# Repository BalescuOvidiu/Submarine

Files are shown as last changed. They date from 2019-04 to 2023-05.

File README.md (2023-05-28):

# Submarin dronă - Clasa Metere

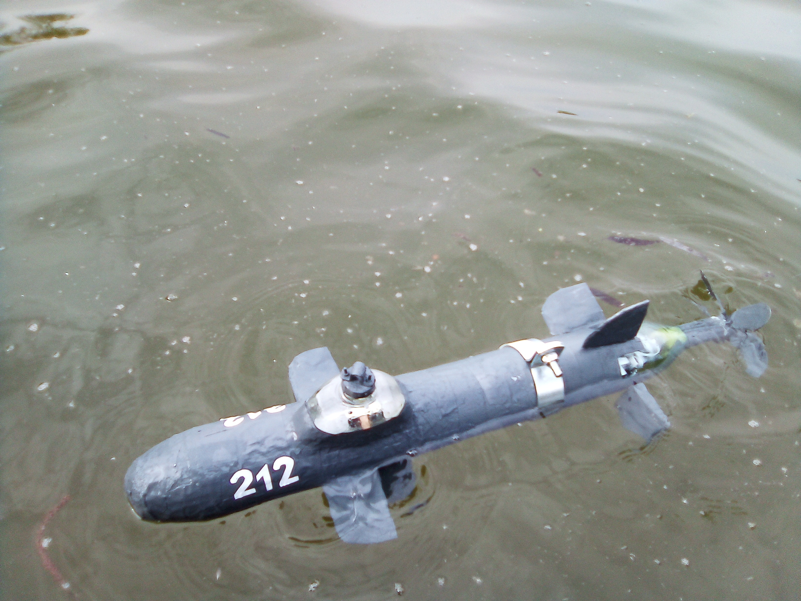
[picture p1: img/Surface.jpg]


## Cuprins

1. [Despre proiect](https://github.com/BalescuOvidiu/Submarine#despre-proiect)<br>
3. [Caracteristici generale](https://github.com/BalescuOvidiu/Submarine#caracteristici-generale)<br>
2. [Structură](https://github.com/BalescuOvidiu/Submarine#structură)<br>
5. [Circuit electric](https://github.com/BalescuOvidiu/Submarine#circuit-electric)<br>
5. [Software](https://github.com/BalescuOvidiu/Submarine#software)<br>
6. [Viitoare îmbunătățiri](https://github.com/BalescuOvidiu/Submarine#viitoare-îmbunătățiri)<br>
7. [Versiuni](https://github.com/BalescuOvidiu/Submarine#versiuni)<br>
7. [Unități](https://github.com/BalescuOvidiu/Submarine#unități)<br>
7. [Teste](https://github.com/BalescuOvidiu/Submarine#teste)<br>
8. [Rezultate](https://github.com/BalescuOvidiu/Submarine#rezultate)<br>

## Despre proiect

<p align = "justify">
Acest proiect e reprezentat de un tip de vehicul mic capabil să meargă prin apă, controlate printr-o telecomandă sau cu un laptop. Scopul acestuia este de a explora spațiul acvatic, de găsi obiecte pierdute în apă sau pentru divertisment.
</p>
<p align = "justify">
O dronă, este un vehicul căruia îi lipsește pilotul uman, fiind ghidat fie de către un pilot automat digital aflat la bordul său, fie prin telecomandă. Un submarin este un vehicul capabil să meargă prin apă la diverse adâncimi și să se ridice la suprafață. Vehiculul acestui proiect este un submarin dronă. 
</p>

## Caracteristici generale

| Nume clasă &nbsp; &nbsp; &nbsp; &nbsp; &nbsp; | Metere  &nbsp; &nbsp; &nbsp; &nbsp; &nbsp; &nbsp; &nbsp; &nbsp; &nbsp; &nbsp; &nbsp; &nbsp; | 
|:---|:---|
| Cost unitate | 2422.34 RON |
| Deplasament | La suprafață: 5.9 kg  <br> În imersie: 7.8 kg |
| Lungime | 102.5 cm |
| Lățime | 10.0 cm |
| Pescaj | 7.5 cm |
| Propulsie | 1 <a href = "https://www.pololu.com/category/60/micro-metal-gearmotors"> motor DC cu reductor 50:1 HPCB 6 V </a><br>1 <a href = "https://en.wikipedia.org/wiki/Pump-jet"> elice cu 7 lame pompă-jet</a> |
| Viteză | 5.2 noduri (9.7 km / h) |
| Autonomie | 3.5 ore |
| Adâncime operațională | 0.5 m (1.6 ft) fără cablu <br> 3.0 m (9.6 ft) cu cablu |
| Adâncime maximă | 10.0 m (65.6 ft) |
| Rază acoperire comunicații | 1000 m (3280.8 ft) la suprafață |
| Sensori și sisteme de procesare | 2 <a href = "https://www.optimusdigital.ro/ro/compatibile-cu-arduino-nano/1686-placa-de-dezvoltare-compatibila-cu-arduino-nano-atmega328p-i-ch340.html" >plăci de dezvoltare Arduino Nano v3</a> <br> 1 <a href = "https://www.optimusdigital.ro/ro/ism-24-ghz/119-modul-nrf24l01-pentru-distante-mari.html" >transceiver nRF24L01</a> <br>1 <a href = "https://www.optimusdigital.ro/ro/senzori-senzori-inertiali/865-modul-senzor-cu-9-axe-mpu9250.html" >IMU MPU9250</a> <br>3 <a href = "https://www.optimusdigital.ro/ro/senzori-senzori-ultrasonici/2943-modul-senzor-ultrasonic-rezistent-la-apa-jsn-sr04t-cu-sonda-pt-masurare-la-distana.html" >senzori de distanță JSN-SR04T</a> |
| Alimentare  | 32 <a href = "https://www.soselectronic.ro/products/conrad-energy/4aa2500mwh1-6v-bp4-1-153207">acumulatori AA de 1.6 V, 1500 mAh</a>  |

## Structură

<p align = "justify">
Denumirea clasei vine de la numele celor două materiale principale folosite la construirea corpului interior: metal(oțel în cazul nostru) și polietilenă tereftalată (PET). Principiul de construire constă în combinarea metalului și plasticului astfel încât structura să fie cât mai rezistentă și cât mai ușoară. Oțelul e rezistent, dar greu și oxidabil. Polietilena tereftalată e ușoară, flexibilă, nu ruginește, dar fragilă.
</p>
<p align = "justify">
PET-ul este o masă plastică folosită de obicei la fabricarea diverselor ambalaje, care în cele din urmă ajung gunoi și contaminează apa cu microplastic. Totuși aceasta poate fi folosită pentru a proteja câteva circuite de apa rece a mării, iar o structură metalică poate oferi o rezistență deosebită ambalajului de plastic.
</p>
<p align = "justify">
Carcasa submarinul este construită din PET și este acoperită cu silicon. Același principiu este aplicat, elicei, cârmelor și hidroplanelor. Siliconul e mult mai rezistent față de cauciuc sau de vopsea și este mult mai ecologic în sensul că nu interacționează cu apa și nu lasă în urmă particule.
</p>
<p align = "justify">
Structura este modulară pentru a fi ușor de reparat. Fiecare compartiment este alcătuit din două capace metalice conectate cu 4 colțare așezate în formă de cruce. Fiecare colțar este conectat cu cel de pe celălalt capac cu o placă de oțel zincat de îmbinare. Toată structura compartimentului este acoperită cu o folie de PET îmbinată de structura metalică cu șuruburi, formând un cilindru sau o semi-sferă. Fiecare compartiment se poate deschide în partea de sus. Cele două capace metalice ale compartimentului au 8 găuri pentru îmbinarea cu alte compartimente și încă 2 găuri pentru fire. Compartimentele sunt conectate cu 4 plăci de îmbinare zincate. Ca si sigilant s-a folosit silicon. Acesta e biodegradabil și rezistent la apă.
</p>

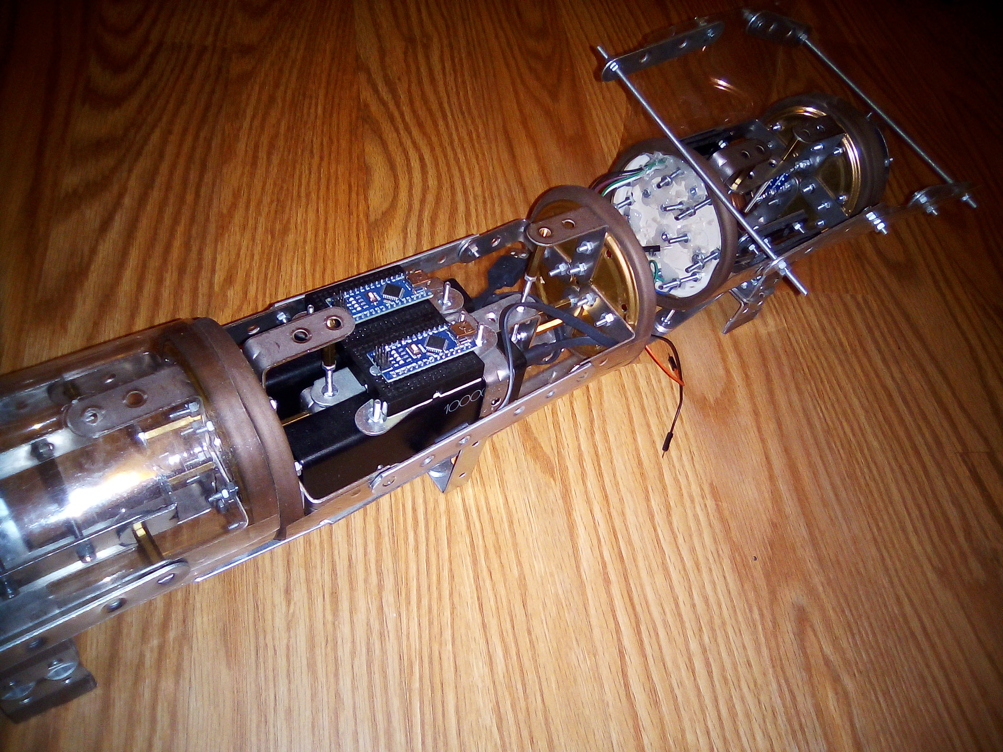
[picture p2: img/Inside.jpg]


#### Compartimente

| &nbsp; &nbsp; # | Compartiment &nbsp; &nbsp; &nbsp; &nbsp; &nbsp; &nbsp; &nbsp; &nbsp; &nbsp; &nbsp; &nbsp; &nbsp; | &nbsp; &nbsp; # | Compartiment &nbsp; &nbsp; &nbsp; &nbsp; &nbsp; &nbsp; &nbsp; &nbsp; &nbsp; &nbsp; &nbsp; &nbsp; &nbsp; &nbsp; &nbsp; &nbsp; &nbsp; &nbsp; |
|----:|:---|----:|:---|
| 1 | Pupa | 5  | Alimentare și circuit central |
| 2 | Compartiment servomotoare | 6  | Control hidroplane față și sistem de orientare |
| 3 | Alimentare circuit motoare și servomotoare | 7  | Provă |
| 4 | Compartiment utilitar | 8  | Corpul de navigare | 

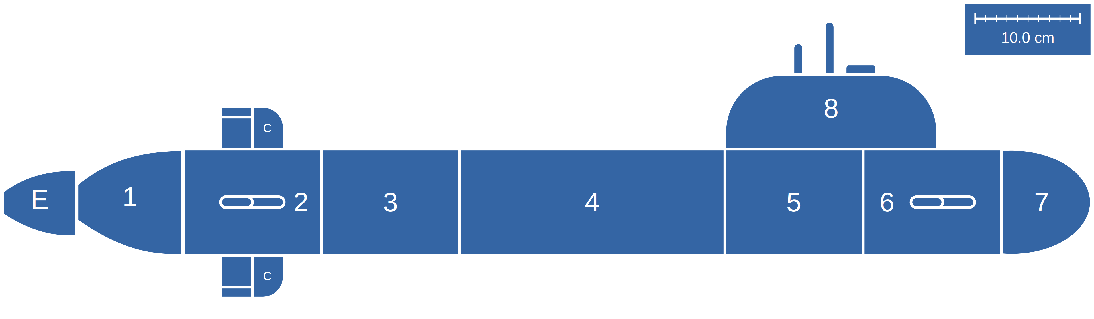
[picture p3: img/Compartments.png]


## Circuit electric
<p align = "justify">
Sunt două surse de alimentare: spate și față. Ambele au un voltaj de 6.0 V. Fiecare sursă este formată din 4 socluri conectate în paralel. Fiecare soclu are 4 acumulatori AA conectați în serie de 1.6 V, 1500 mAh.
</p>
<p align = "justify">
Cele două plăci Arduino sunt alimentate de sursa din față. Alimentarea pentru plăci poate fi oprită sau pornită dintr-un comutator. Senzorii și modulele auxiliare sunt conectate la sursele de alimentarea al celor două plăci Arduino, la 3.3 V sau 5.0 V în funcție de nevoi. Motoarele sunt conectate la sursa din spate, mai puțin servomotorul din față care e alimentat de sursa din față. Alimentarea motoarelor este controlată printr-un tranzistor pentru fiecare. Tranzistorul primește semnal de la placa Arduino dacă să oprească sau să pornească alimentarea.
</p>

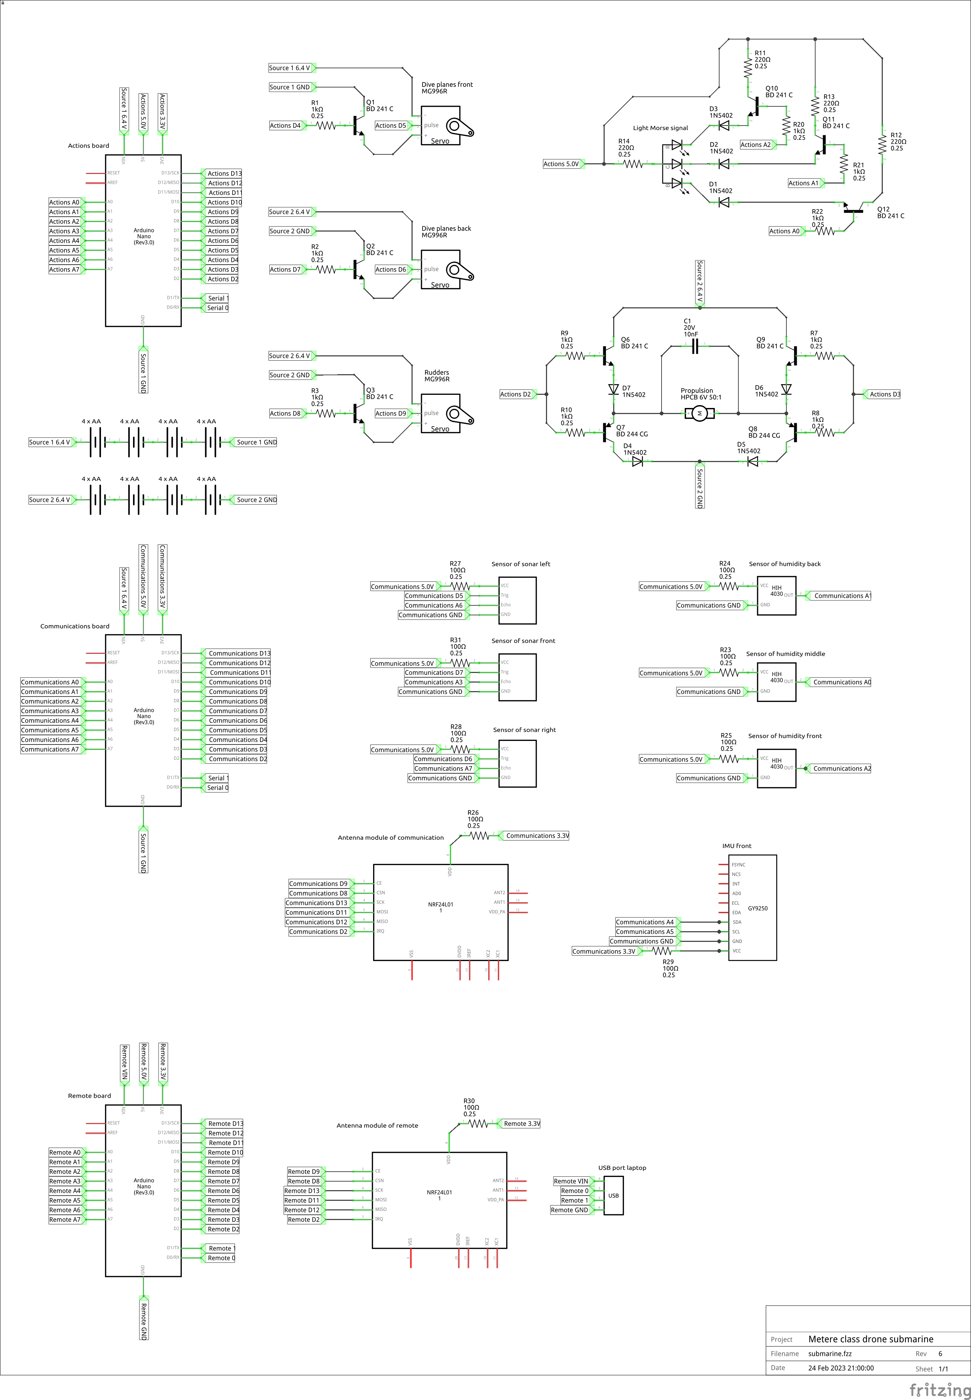
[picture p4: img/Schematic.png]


## Software
<p align = "justify">
Programele pentru plăcile <a href = "https://www.arduino.cc/">Arduino</a> de pe vehicul și telecomandă au fost scrise în C++ pentru arhitectura ARV, microcontrolere.</p>
<p align = "justify">
Interfața grafică a fost scrisă în limbajul <a href = "http://www.cplusplus.com/">C++ 11</a> și au fost folosite framework-urile: <a href = "https://www.sfml-dev.org/">SFML 2.5.1</a> și <a href = "https://github.com/nlohmann/json">Nlohmann JSON</a>. Aceasta are scopul de a vizualiza datele de la senzorii submarinului și de controla componentele de pe acesta.</p>

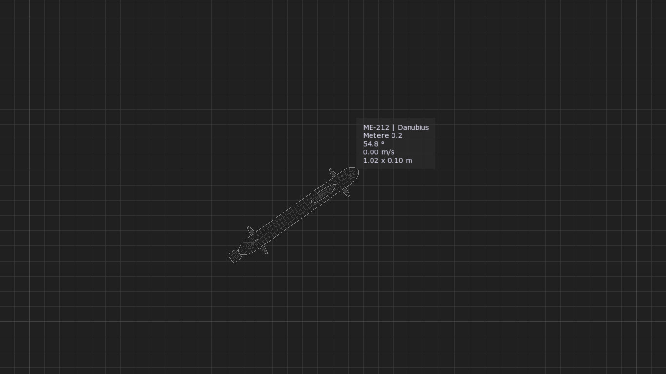
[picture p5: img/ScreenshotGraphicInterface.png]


#### Cerințe minime sistem pentru interfață
1. Procesor DualCore 2.0 GHz,
2. DDR2 RAM 2G,
3. Placă video 256MB,
4. Sistem de operare Linux, Windows sau Mac. 

## Viitoare îmbunătățiri
1. Optimizare și îmbunătățire software,
2. Optimizare consum de energie,
3. Extindere rază și adâncime acoperire comunicații,
4. Instalare cameră pe corpul de navigare,
5. Instalare generator din cupru și aluminiu pentru alimentarea acumulatorilor.

## Versiuni

| # | Data | Descriere |
|--:|:---|:---|
| 0.2 | 20 Octombrie 2019 | Compartimentele au fost restructurate și etanșate separat. Carcasa din PET a fost reconstruită și acoperită cu silicon. La fel și aripile. Propulsia cu elice 7 lame a fost înlocuită cu elice cu 7 lame pompă-jet.<br> Servomotoarele <a href="https://www.optimusdigital.ro/ro/motoare-servomotoare/271-servomotor-mg90s.html">MG90S</a> montate anterior au fost înlocuite cu <a href="https://www.optimusdigital.ro/ro/motoare-servomotoare/1160-servomotor-metalic-digital-mg996.html">MG996</a> și s-a adăugat unul pentru planele de scufundare din față. <br> Receptorul infrarosu a fost înlocuit cu un modul <a href = "https://www.optimusdigital.ro/ro/ism-24-ghz/119-modul-nrf24l01-pentru-distante-mari.html" >transceiver nRF24L01</a>. Bateriile AA de 1.5V au fost înlocuite cu <a href = "https://www.soselectronic.ro/products/conrad-energy/4aa2500mwh1-6v-bp4-1-153207">acumulatori AA de 1.6 V, 1500 mAh</a>. <br> S-au adăugat: trei senzori de umiditate pentru detectatarea scurgeriilor, un sistem pe bază de tranzistori bipolari de putere pentru controlul surselor de alimentare al motoarelor, un <a href = "https://www.optimusdigital.ro/ro/senzori-senzori-inertiali/865-modul-senzor-cu-9-axe-mpu9250.html" >IMU MPU9250</a> și 3 senzori ultrasonici de distanță <a href = "https://www.optimusdigital.ro/ro/senzori-senzori-ultrasonici/2943-modul-senzor-ultrasonic-rezistent-la-apa-jsn-sr04t-cu-sonda-pt-masurare-la-distana.html" >JSN-SR04T</a>. |
| 0.1 | 1 Ianuarie 2019 | Prima versiune. |

## Unități

<p align = "justify">
În momentul actual proiectul este în faza experimentală și se urmărește dezvoltarea doar unei singure unități.
</p>

| # | Nume | Versiune | Lansare | Începerea construcției | Dezvoltator | Status |
|:----|:---|:---|:---|:---|:---|:---|
| ME-212 | Danubius | 0.1 | 16 Aprilie 2019 | 1 Ianuarie 2019 | Bălescu Ovidiu-Gheorghe | În construcție pentru a trece la versiunea 0.2 |

## Teste

#### Testare versiunea 0.1 - 16 Aprilie 2019 
<p align = "justify">
S-a desfășurat pe lacul din Parcul Tineretului, București. S-a deplasat fără probleme la suprafața apei, dar nu a reușit să execute o submersie. 
Problema era cauzată de planele de scufundare din față, fiind fixate(nu erau conectate la un motor, ci doar lipite). Asta nu a permis să încline submarinul cu botul în jos și să execute o submersie dinamică. Carcasa din PET acoperită cu lac de lemn nu a permis apei să intre, dar în urma unor șocuri mecanice s-a observat că lacul întărit se desprinde de pe plastic.
Click <a href = "https://drive.google.com/file/d/1TcdASmKPXG35pqwhGr6TglmWBqajAN5j/view?usp=share_link" >aici</a> pentru a vedea filmarea. 
</p>

## Rezultate

#### Proiect la cursul de Introducere în Robotică, anul universitar 2018 - 2019

| Universitatea București &nbsp; &nbsp; &nbsp; &nbsp; &nbsp; &nbsp; &nbsp; &nbsp; &nbsp; &nbsp; &nbsp; &nbsp; &nbsp; &nbsp; | Facultatea de Matematică și Informatică &nbsp; &nbsp; &nbsp; &nbsp; &nbsp; &nbsp; &nbsp; &nbsp; &nbsp; &nbsp; &nbsp; &nbsp; &nbsp; &nbsp; &nbsp; &nbsp; &nbsp; |
|:---|:---|
| Profesor coordonator | Dumitriu Andrei |
| Laborant | Octavia Ivona |
| Student | Bălescu Ovidiu-Gheorghe |
| Notă evaluare | 10 / 10 |

#### Proiect prezentat la Sesiunea de comunicări Științifice Studențești - 2019

| Universitatea București &nbsp; &nbsp; &nbsp; &nbsp; &nbsp; &nbsp; &nbsp; &nbsp; &nbsp; &nbsp; &nbsp; &nbsp; &nbsp; &nbsp; | Facultatea de Matematică și Informatică &nbsp; &nbsp; &nbsp; &nbsp; &nbsp; &nbsp; &nbsp; &nbsp; &nbsp; &nbsp; &nbsp; &nbsp; &nbsp; &nbsp; &nbsp; &nbsp; &nbsp; |
|:---|:---|
| Profesor coordonator | Dumitriu Andrei |  
| Student | Bălescu Ovidiu-Gheorghe |
| Loc | II |

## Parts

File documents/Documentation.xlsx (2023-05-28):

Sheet: Centralizare
Componentă | Cost | Masă |  | Viteză |  | Distanța maximă parcusă |  | Volum | Densitate lichid | Înălțime | Masă | Masă maximă | Pescaj
Circuit | 1374.34 RON | 1764.59 g | 2 | 270.00 | cm/s | 3588923.08 | cm | 0.007856 mc | 1000.00 kg/mc | 0.10 m | 5.901280 kg | 7.855638 kg | 0.075 m
Structură | 858.00 RON | 3011.69 g | 4 | 2.70 | m/s | 35889.23 | m
Carcasă | 190.00 RON | 1125.00 g | 6 | 9.72 | km/h | 35.89 | km
Vehicul | 2422.34 RON | 5901.28 g |  | 5.24 | noduri | 2.82 | mile marine
Telecomandă | 56.00 RON | 125.00 g
Total | 2478.34 RON | 6026.28 g

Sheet: Rezistență
Componentă | Lungime | Lățime | Suprafață | Volum | Suprafață coloană lichid | Masă maximă suportată | Adâncime maximă
Compartiment 1 – Provă | 0.100 m | 0.100 m | 0.015708 m^2 | 0.000589 mc | 0.010000 m^2 | 120.00 kg | 12.00 m
Compartiment 2 | 0.130 m | 0.100 m | 0.020420 m^2 | 0.001021 mc | 0.013000 m^2 | 160.00 kg | 12.31 m
Compartiment 3 | 0.130 m | 0.100 m | 0.020420 m^2 | 0.001021 mc | 0.013000 m^2 | 160.00 kg | 12.31 m
Compartiment 4 | 0.250 m | 0.100 m | 0.039270 m^2 | 0.001963 mc | 0.025000 m^2 | 250.00 kg | 10.00 m
Compartiment 5 | 0.130 m | 0.100 m | 0.020420 m^2 | 0.001021 mc | 0.013000 m^2 | 160.00 kg | 12.31 m
Compartiment 6 | 0.130 m | 0.100 m | 0.020420 m^2 | 0.001021 mc | 0.013000 m^2 | 200.00 kg | 15.38 m
Compartiment 7 – Pupă | 0.085 m | 0.100 m | 0.053407 m^2 | 0.000056 mc | 0.008500 m^2 | 85.00 kg | 10.00 m
Compartiment 8 – Corpul de navigație | 0.200 m | 0.070 m | 0.021991 m^2 | 0.000840 mc | 0.014000 m^2 | 150.00 kg | 10.71 m
Elice | 0.070 m | 0.070 m | 0.007697 m^2 | 0.000269 mc | 0.004900 m^2 | 50.00 kg | 10.20 m
Cârme | 0.030 m | 0.010 m | 0.000300 m^2 | 0.000018 mc | 0.000300 m^2 | 3.00 kg | 10.00 m
Plane de scufundare față | 0.060 m | 0.030 m | 0.001800 m^2 | 0.000018 mc | 0.001800 m^2 | 20.00 kg | 11.11 m
Plane de scufundare spate | 0.060 m | 0.030 m | 0.001800 m^2 | 0.000018 mc | 0.001800 m^2 | 20.00 kg | 11.11 m
 | 0.955 m | 0.160 m |  | 0.007856 mc |  |  | 10.00 m

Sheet: Alimentare
Componentă |  |  | Voltaj |  |  |  | Capacitate |  |  |  | Utilitate |  | Autonomie
Nume | Voltaj | Consum | Acumulator 1 | Acumulator 2 | Acumulator 3 | Acumulator 4 | Acumulator 1 | Acumulator 2 | Acumulator 3 | Acumulator 4 | Voltaj acoperit | Capacitate | Consum | Alimentare | 3.69
Micromotor 50:1 HPCB – Elice | 6.00 V | 300.00 mAh | 1.60 V | 1.60 V | 1.60 V | 1.60 V | 1500.00 mAh | 1500.00 mAh | 1500.00 mAh | 1500.00 mAh | 6.40 V | 1500.00 mAh | 1300.00 | 6000.00 | 3.69
Servomotor – Cârmă | 6.00 V | 500.00 mAh | 1.60 V | 1.60 V | 1.60 V | 1.60 V | 1500.00 mAh | 1500.00 mAh | 1500.00 mAh | 1500.00 mAh | 6.40 V | 1500.00 mAh
Servomotor – Hidroplane spate | 6.00 V | 500.00 mAh | 1.60 V | 1.60 V | 1.60 V | 1.60 V | 1500.00 mAh | 1500.00 mAh | 1500.00 mAh | 1500.00 mAh | 6.40 V | 1500.00 mAh
 |  |  | 1.60 V | 1.60 V | 1.60 V | 1.60 V | 1500.00 mAh | 1500.00 mAh | 1500.00 mAh | 1500.00 mAh | 6.40 V | 1500.00 mAh
Nume | Voltaj | Consum | Acumulator 1 | Acumulator 2 | Acumulator 3 | Acumulator 4 | Acumulator 1 | Acumulator 2 | Acumulator 3 | Acumulator 4 | Voltaj acoperit | Capacitate | Consum | Alimentare | 4.36
Servomotor – Hidroplane față | 6.00 V | 500.00 mAh | 1.60 V | 1.60 V | 1.60 V | 1.60 V | 1500.00 mAh | 1500.00 mAh | 1500.00 mAh | 1500.00 mAh | 6.40 V | 1500.00 mAh | 1100.00 | 6000.00 | 4.36
Arduino Nano V3 | 6.00 V | 300.00 mAh | 1.60 V | 1.60 V | 1.60 V | 1.60 V | 1500.00 mAh | 1500.00 mAh | 1500.00 mAh | 1500.00 mAh | 6.40 V | 1500.00 mAh
Arduino Nano V3 | 6.00 V | 300.00 mAh | 1.60 V | 1.60 V | 1.60 V | 1.60 V | 1500.00 mAh | 1500.00 mAh | 1500.00 mAh | 1500.00 mAh | 6.40 V | 1500.00 mAh
 |  |  | 1.60 V | 1.60 V | 1.60 V | 1.60 V | 1500.00 mAh | 1500.00 mAh | 1500.00 mAh | 1500.00 mAh | 6.40 V | 1500.00 mAh

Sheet: Pini
 | $B$4:$B$100 |  | $D$4:$D$100 |  | $F$4:$F$100 |  | $H$4:$H$100 | 4 | 100
Conexiuni pini | 34 |  | 19 |  | 15 |  | 6
Nume componentă | Număr pini |  | Communications |  | Actions |  | Remote
Comunicații serial | 2 | 1 | 2 | 1 | 2 |  | 0
LED RGB | 3 | 0 | 0 | 1 | 3 |  | 0
Modul cu atenă NRF 24L01 | 6 | 1 | 6 | 0 | 0 | 1 | 6
Micromotor cu reductor 50 la 1 HPCB 6 V cu ax lung | 2 | 0 | 0 | 1 | 2 |  | 0
Senzor de distanța ultrasonic JSN-SR04T | 2 | 3 | 6 | 0 | 0 |  | 0
Senzor de umiditate | 1 | 3 | 3 | 0 | 0 |  | 0
Senzor inerțial MPU9250 | 2 | 1 | 2 | 0 | 0 |  | 0
Senzor micromotor HPCB 6 V cu ax lung | 2 | 0 | 0 | 1 | 2 |  | 0
Servomotor MG996R 60 | 2 | 0 | 0 | 3 | 6 |  | 0

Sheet: Circuit
 | $B$4:$B$100 | $C$4:$C$100 | $D$4:$D$100 | $E$4:$E$100 | $F$4:$F$100 | 4 | 100
Circuit | 107 | 18.14 RON | 1374.34 RON | 15.02 g | 1764.59 g
Nume | Cantitate | Preț unitate | Preț total | Masă unitate | Masă totală
Acumulator 1.6V 1500 mAh AA ConradEnergy | 16 | 11.80 RON | 188.80 RON | 30.00 g | 480.00 g
Acumulator 1.6V 1500 mAh AA Ansmann | 16 | 24.00 RON | 384.00 RON | 31.00 g | 496.00 g
Mini Breadboard negru | 4 | 2.36 RON | 9.44 RON | 14.00 g | 56.00 g
Placă de dezvoltare Arduino Nano V3 | 2 | 20.00 RON | 40.00 RON | 17.00 g | 34.00 g
Comutator LED KCD10-101 | 1 | 2.00 RON | 2.00 RON | 13.00 g | 13.00 g
Condensator 10 nF 20 V | 1 | 0.10 RON | 0.10 RON | 0.10 g | 0.10 g
Diodă 1N5402 | 7 | 0.10 RON | 0.70 RON | 0.01 g | 0.07 g
LED RGB cu catod comun | 1 | 1.00 RON | 1.00 RON | 0.01 g | 0.01 g
Modul cu atenă NRF 24L01 | 1 | 25.00 RON | 25.00 RON | 30.00 g | 30.00 g
Motor HPCB Pololu 50:1 6 V | 1 | 77.00 RON | 77.00 RON | 10.00 g | 10.00 g
Rezistor 100 ohm | 7 | 0.10 RON | 0.70 RON | 0.01 g | 0.07 g
Rezistor 1000 ohm | 10 | 0.10 RON | 1.00 RON | 0.01 g | 0.10 g
Rezistor 220 ohm | 4 | 0.10 RON | 0.40 RON | 0.01 g | 0.04 g
Senzor de distanța ultrasonic JSN-SR04T | 3 | 124.00 RON | 372.00 RON | 50.00 g | 150.00 g
Senzor inerțial MPU9250 | 1 | 47.00 RON | 47.00 RON | 5.00 g | 5.00 g
Senzor umiditate | 3 | 4.00 RON | 12.00 RON | 20.00 g | 60.00 g
Servomotor MG996 60 | 3 | 20.00 RON | 60.00 RON | 55.00 g | 165.00 g
Set fire mufate | 6 | 10.00 RON | 60.00 RON | 28.00 g | 168.00 g
Soclu baterii 4 x AA pătrat | 8 | 10.00 RON | 80.00 RON | 12.00 g | 96.00 g
Tranzistor NPN BD 241 C | 10 | 1.10 RON | 11.00 RON | 0.10 g | 1.00 g
Tranzistor PNP BD 244 CG | 2 | 1.10 RON | 2.20 RON | 0.10 g | 0.20 g

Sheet: Structură
 | $B$4:$B$100 | $C$4:$C$100 | $D$4:$D$100 | $E$4:$E$100 | $F$4:$F$100 | 4 | 100 | 12
Structură | 1669 | 4.03 RON | 858.00 RON | 21.60 g | 3011.69 g
Nume | Cantitate | Preț unitate | Preț total | Masă unitate | Masă totală
Bandă asamblare oțel zincat 60 mm | 0 | 1.00 RON |  | 11.25 g
Bandă asamblare oțel zincat 80 mm | 36 | 1.00 RON | 36.00 RON | 15.00 g | 540.00 g
Bandă asamblare oțel zincat 200 mm | 4 | 2.00 RON | 8.00 RON | 50.00 g | 200.00 g
Capac borcan metalic auriu 90 mm | 12 | 0.30 RON | 3.60 RON | 12.50 g | 150.00 g
Conector L dreapta Zinc 30x40x1 mm | 4 | 3.00 RON | 12.00 RON | 0.75 g | 3.00 g
Conector unghi Zinc 30x30x15 mm | 72 | 3.00 RON | 216.00 RON | 10.75 g | 774.00 g
Cornier Negru cu Șuruburi pentru Motoarele N20 | 1 | 2.00 RON | 2.00 RON | 11.00 g | 11.00 g
Silicon 300ml negru | 3 | 60.00 RON | 180.00 RON | 300.00 g | 900.00 g
Magnet adeziv disc 12 mm | 14 | 2.00 RON | 28.00 RON | 5.00 g | 70.00 g
PET 1.5 l | 12 | 1.00 RON | 12.00 RON | 20.00 g | 240.00 g
Pilon M3 18 mm | 2 | 1.75 RON | 3.50 RON | 3.50 g | 7.00 g
Pilon M3 25 mm | 2 | 2.45 RON | 4.90 RON | 5.00 g | 10.00 g
Piuliță M3 hexagonală | 646 | 0.25 RON | 161.50 RON | 0.06 g | 38.76 g
Piuliță M3 hexagonală autoblocantă | 0 | 0.49 RON |  | 0.06 g
Șaibă M3 | 406 | 0.20 RON | 81.20 RON | 0.03 g | 12.18 g
Șuruburi M3 8 mm cap înecat | 96 | 0.20 RON | 19.20 RON | 0.06 g | 6.00 g
Șuruburi M3 8 mm cap rotund | 48 | 0.20 RON | 9.60 RON | 0.06 g | 3.00 g
Șuruburi M3 16 mm cap înecat | 310 | 0.25 RON | 77.50 RON | 0.12 g | 38.75 g
Șuruburi M3 25 mm cap rotund | 0 | 0.25 RON |  | 0.20 g
Șuruburi M3 45 mm cap rotund | 0 | 0.29 RON |  | 0.35 g
Tijă filetată M3 1 m | 1 | 3.00 RON | 3.00 RON | 8.00 g | 8.00 g

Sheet: Carcasă
 | $B$4:$B$100 | $C$4:$C$100 | $D$4:$D$100 | $E$4:$E$100 | $F$4:$F$100 | 4 | 100
Carcasă | 13 | 30.50 RON | 190.00 RON | 161.25 g | 1125.00 g
Nume | Cantitate | Preț unitate | Preț total | Masă unitate | Masă totală
Silicon 300ml negru | 3 | 60.00 RON | 180.00 RON | 300.00 g | 900.00 g
PET 1.5 L | 10 | 1.00 RON | 10.00 RON | 22.50 g | 225.00 g

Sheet: Telecomandă
 | $B$4:$B$100 | $C$4:$C$100 | $D$4:$D$100 | $E$4:$E$100 | $F$4:$F$100 | 4 | 100
Telecomandă | 4 | 14.00 RON | 56.00 RON | 31.25 g | 125.00 g
Nume | Cantitate | Preț unitate | Preț total | Masă unitate | Masă totală
Placă de dezvoltare Arduino Nano V3 | 1 | 20.00 RON | 20.00 RON | 17.00 g | 17.00 g
Modul cu atenă NRF 24L01 | 1 | 25.00 RON | 25.00 RON | 30.00 g | 30.00 g
Set fire mufate | 1 | 10.00 RON | 10.00 RON | 28.00 g | 28.00 g
PET 1.5 L | 1 | 1.00 RON | 1.00 RON | 50.00 g | 50.00 g

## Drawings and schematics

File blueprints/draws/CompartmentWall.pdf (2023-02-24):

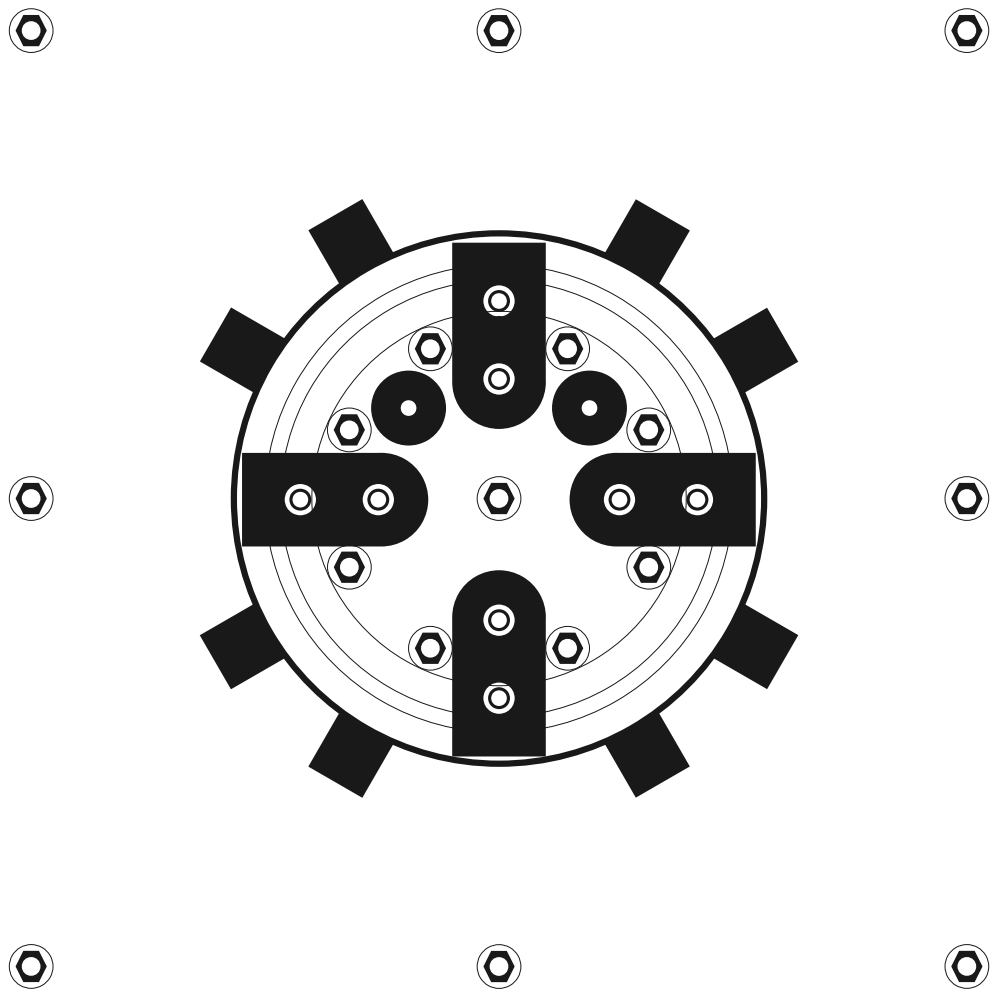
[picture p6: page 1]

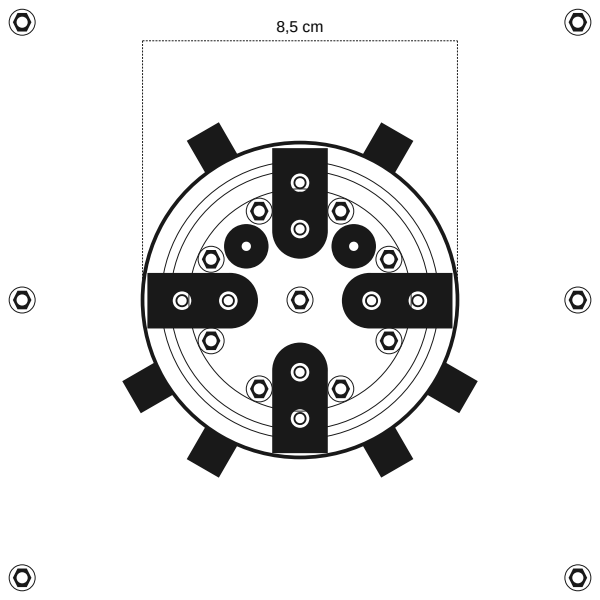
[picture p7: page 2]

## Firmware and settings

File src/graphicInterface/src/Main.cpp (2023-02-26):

/**
 *  Main.h
 * 
 *  Created 15 May 2019
 *  By Balescu Ovidiu-Gheorghe
 *  Modified 22 February 2023
 *  By Balescu Ovidiu-Gheorghe
 */

#include "Log.h"
#include "Ruller.h"
#include "Writer.h"
#include "ControlPanel.h"
#include "Utils.h"

#define DEFAULT_CONFIG_FILE_DIRECTORY "config.json"

/**
 * This function run the program. It initializes GUI 
 * objects and data, run execution loop and stop the
 * execution.
 */
int main () {
	json config = getJsonFromFile (DEFAULT_CONFIG_FILE_DIRECTORY);

	Log::initialize ();
	Ruller::initialize ();
	Writer::initialize (config["fontFile"]);
	Component::initialize ();

	Log::write ("Screen size: " + Writer::toString (Ruller::size (), 0, " x ") + ".");
	
	sf::RenderWindow window (
		sf::VideoMode ().getDesktopMode (), 
		sf::String ((std::string)config["windowTitle"]), 
		sf::Style::Fullscreen
	);
	Log::write ("The window is open.");
	if (config["verticalSyncEnabled"]) {
		window.setVerticalSyncEnabled(config["verticalSyncEnabled"]);
		Log::write ("The Vertical Sync is enabled.");
	}
	else {
		window.setFramerateLimit(config["framerate"]);
		Log::write ("The framerate is fixed.");
	}
	sf::View view (
		sf::FloatRect (0, 0, Ruller::width (), Ruller::height ())
	);

	ControlPanel panel (&window, &view);
	panel.loadShip (config["selectedShipFile"]);

	while (window.isOpen ()) {

		/** Event */
		sf::Event event;
		while (window.pollEvent (event)) {
			if (event.type == sf::Event::Closed) {
				window.close();
			}
		}

		/** Draw. */
		window.clear ();

		panel.render (&window);
		panel.update (&window, &view);

		window.display ();

		/** Check for the close */
		if (panel.isClosed ()) {
			window.close ();
		}
	}

	/** Closing */
	Log::write ("Close!");
	Log::close();

	return EXIT_SUCCESS;
}

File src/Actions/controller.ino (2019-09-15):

#include "controller.h"

// Variables used for control.
static bool flood = false;
static byte humidityLimit = 100;
static unsigned timeTest = 200;

// Objects used to control motors.
Motor propeller (PIN_PROPELLER_A, PIN_PROPELLER_B);
Motor ballast (PIN_BALLAST_A, PIN_BALLAST_B);

// Objects used to control rudders and planes.
Servomotor rudderBottom;
Servomotor rudderTop;
Servomotor planeLeft;
Servomotor planeRight;

// Objects used for communications.
IrDevice irReceiver (PIN_IR_RECEIVER);

/**
 * This function stops move of rudders and planes
 * and sets them on middle angle.
 */
void stabilize () {
  rudderBottom.disableTest ();
  rudderTop.disableTest ();
  planeLeft.disableTest ();
  planeRight.disableTest ();
  
  rudderBottom.middle ();
  rudderTop.middle ();
  planeLeft.middle ();
  planeRight.middle ();
}

/**
 * This function stop motors and
 * stabilize the servomotors.
 */
void wait () {
  propeller.stop ();
  ballast.stop ();
  stabilize ();
}

/**
 * This function sets angle of rudders.
 * 
 * @param angle new orientation of servomotors.
 */
void setRudderAngle (int angle) {
  rudderBottom.write (ANGLE_MIDDLE - angle);
  rudderTop.write (ANGLE_MIDDLE + angle);
}

/**
 * This function sets angle of planes.
 * 
 * @param: angle new orientation of servomotors.
 */
void setPlaneAngle (int angle) {
  planeLeft.write (ANGLE_MIDDLE + angle);
  planeRight.write (ANGLE_MIDDLE - angle);
}

/**
 * This function maintain angle of rudders and planes.
 */
void loopServo () {
  rudderBottom.loop ();
  rudderTop.loop ();
  planeLeft.loop ();
  planeRight.loop ();
}

/**
 * This function makes links between 
 * communication with hardware parts.
 */
void command() {
  // Infra-red communication
  unsigned long value = irReceiver.check();
  if (value) {
    Serial.print ("Command: ");
    Serial.println (value, HEX);
    irReceiver.resume ();
    
    switch (value) {
      // Propeller speed
      case C_FASTER:
        propeller.increaseVelocity (RATE_MEDIUM);
        break;
      case C_SLOWER:
        propeller.decreaseVelocity (RATE_MEDIUM);
        break;
      case C_STOP:
        propeller.stop ();
        break;
      case C_WAIT:
        wait ();
        break;
      // Direction and angle
      case C_LEFT:
        setRudderAngle (ANGLE_ACUTE);
        break;
      case C_RIGHT:
        setRudderAngle (-ANGLE_ACUTE);
        break;
      case C_DOWN:
        setPlaneAngle (-ANGLE_ACUTE);
        break;
      case C_UP:
        setPlaneAngle (ANGLE_ACUTE);
        break;
      case C_STABILIZE:
        stabilize ();
        break;
      // Test of servomotors
      case C_TEST_RUDDER_BOTTOM:
        rudderBottom.toggleTest (timeTest);
        break;
      case C_TEST_RUDDER_TOP:
        rudderTop.toggleTest (timeTest);
        break;
      case C_TEST_PLANE_LEFT:
        planeLeft.toggleTest (timeTest);
        break;
      case C_TEST_PLANE_RIGHT:
        planeRight.toggleTest (timeTest);
        break;      
    }
  }

  // Check of humidity inside of submarine.
  if (analogRead (PIN_SENSOR_HUMIDITY) > humidityLimit) {
    flood = true;
  }
  else {
    flood = false;
  }
}

/**
 * This function is called at 
 * initialization of Arduino Board.
 */
void setup() {
  rudderBottom.attach (PIN_RUDDER_BOTTOM);
  rudderTop.attach (PIN_RUDDER_TOP);
  planeLeft.attach (PIN_PLANE_LEFT);
  planeRight.attach (PIN_PLANE_RIGHT);
  
  
  wait();

  unsigned long standardValue[] = {
    C_FASTER,
    C_SLOWER,
    C_STOP,
    C_WAIT,
    C_LEFT,
    C_RIGHT,
    C_DOWN,
    C_UP,
    C_STABILIZE,
    C_TEST_RUDDER_TOP,
    C_TEST_RUDDER_BOTTOM,
    C_TEST_PLANE_LEFT,
    C_TEST_PLANE_RIGHT    
  };
  
  irReceiver.enableIRIn ();
  irReceiver.setInputLoopTime (INPUT_CICLE_MEDIUM);
  irReceiver.setStandardValue (
    standardValue, 
    sizeof (standardValue) / sizeof (standardValue[0])
  );

  Serial.begin(9600);
}

/**
 * This function runs until Arduino Board is stopped.
 */
void loop() {
  propeller.loop();
  loopServo();
   
  command();
}

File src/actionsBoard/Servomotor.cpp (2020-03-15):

/**
 *  Servomotor.cpp
 *
 *  Created 1s May 2019
 *  By Balescu Ovidiu-Gheorghe
 *  Modified 13 February 2020
 *  By Balescu Ovidiu-Gheorghe
 */

#include "Servomotor.h"

/**
 *  This is constructor of class without parameters.
 *  This initialize important parameters with default values.
 */
Servomotor::Servomotor () {
    this->minAngle = 0;
    this->maxAngle = 180;
    this->dutyCycleTime.restart(20);
}

/**
 *  @brief: This is constructor of class. Calls functions 
 *  used to initialize important parameters.
 *  
 *  @param: minAngle - minimum possible rotation angle of servomotor physic part;
 *  @param: maxAngle - maximum possible rotation angle of servomotor physic part;
 *  @param: dutyCycleTime - time between two changes of angle.
 */
Servomotor::Servomotor (short minAngle, short maxAngle, long dutyCycleTime) {
    this->minAngle = minAngle;
    this->maxAngle = maxAngle;

    this->dutyCycleTime.restart (dutyCycleTime);

    this->rotateToMidAngle ();
}

/**
 *  @brief: This is destructor of class.
 */
Servomotor::~Servomotor () {

}

/**
 *  @brief: Initialize importants parameters of servomotor controller.
 *  
 *  @param: minAngle - minimum possible rotation angle of servomotor physic part;
 *  @param: maxAngle - maximum possible rotation angle of servomotor physic part;
 *  @param: dutyCycleTime - time between two changes of angle.
 */
void Servomotor::setup (short minAngle, short maxAngle, long dutyCycleTime) {
    this->setMinAngle (minAngle);
    this->setMaxAngle (maxAngle);

    this->dutyCycleTime.restart (dutyCycleTime);
}

/**
 *  @brief: This function sends signal to mantain angle of electronic
 *  device, respecting the duty cycle time.
 */
void Servomotor::loop () {
    if (this->dutyCycleTime.elapse ()) {
        this->write (this->lastAngle);
    }
}

/**
 *  @brief: This method set new value of minimum angle.
 *
 *  @param: value - new value of minimum angle.
 */
void Servomotor::setMinAngle (short value) {
    if (this->maxAngle > value) {
        this->minAngle = value;
        
        if (this->minAngle > lastAngle) {
            this->rotateToMinAngle ();
        }
    }

}

/**
 *  @brief: This method set new value of maximum angle.
 *
 *  @param: value - new value of maximum angle.
 */
void Servomotor::setMaxAngle (short value) {
    if (this->minAngle < value) {
        this->maxAngle = value;

        if (this->maxAngle < lastAngle) {
            this->rotateToMaxAngle ();
        }
    }
}

/**
 *  @brief: This method set new value of duty cycle time.
 *
 *  @param: value - new value of duty cycle time.
 */
void Servomotor::setDutyCicleTime (unsigned long duration) {
    if (0 < duration) {
        this->dutyCycleTime.restart (duration);
    }
}

/**
 *  @brief: This function sends a signal to decrease angle of
 *  electronic device with a value or until of his limit.
 * 
 *  @param: rate - value low from angle.
 */
void Servomotor::decreaseAngle (short rate) {
   if  (this->minAngle <= this->lastAngle - rate) {
      this->rotateTo (this->lastAngle - rate);
   }
   else {
      this->rotateTo (this->minAngle);
   }
}

/**
 *  @brief: This function sends a signal to increase angle of
 *  electronic device with a value or until of his limit.
 *  
 *  @param: rate - value added to angle.
 */
void Servomotor::increaseAngle (short rate) {
   if  (this->maxAngle >= this->lastAngle + rate) {
      this->rotateTo (this->lastAngle + rate);
   }
   else {
      this->rotateTo (this->maxAngle);
   }
}

/**
 *  @brief: This method sends signal to rotate mechanical
 *  part to a specific angle.
 *
 *  @param: angle - new value in buffer.
 */
void Servomotor::rotateTo (short angle) {
    this->lastAngle = angle;
}

/**
 *  @brief: This method sends signal to rotate mechanical
 *  part to minimum angle.
 */
void Servomotor::rotateToMinAngle () {
    this->rotateTo (this->minAngle);
}

/**
 *  @brief: This method sends signal to rotate mechanical
 *  part to middle angle.
 */
void Servomotor::rotateToMidAngle () {
    this->rotateTo (this->getMidAngle ());
}

/**
 *  @brief: This method sends signal to rotate mechanical
 *  part to maximum angle.
 */
void Servomotor::rotateToMaxAngle () {
    this->rotateTo (this->maxAngle);
}

/**
 *  This function return last value send to servo.
 * 
 *  @return: last value sends to the electronic device.
 */
short Servomotor::getLastAngle () {
   return this->lastAngle;
}

/**
 *  This function returns error of servo rotation electronic device.
 *  
 *  @return: difference between last angle value send to device and 
 *  current angle of device. If that is zero, then servomotor is precise.
 */
short Servomotor::getError () {
   return  this->lastAngle - this->read ();
}

/**
 *  @brief: This method returns min angle rotation of servomotor.
 *
 *  @return: min angle rotation of servomotor..
 */
short Servomotor::getMinAngle () {
    return this->minAngle;
}

/**
 *  @brief: This method returns middle angle rotation of servomotor.
 *
 *  @return: middle angle rotation of servomotor..
 */
short Servomotor::getMidAngle () {
    return 1 >> (this->minAngle + this->maxAngle);
}

/**
 *  @brief: This method returns max angle rotation of servomotor.
 *
 *  @return: max angle rotation of servomotor.
 */
short Servomotor::getMaxAngle () {
    return this->maxAngle;
}

/**
 *  @brief: This method returns duration of duty cycle time.
 *
 *  @return: duration of duty cycle time.
 */
unsigned long Servomotor::getDutyCycle () {
    return this->dutyCycleTime.getDuration ();
}

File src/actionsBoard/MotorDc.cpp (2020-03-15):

/**
 *  MotorDc.cpp
 *
 *  Created 1s May 2019
 *  By Balescu Ovidiu-Gheorghe
 *  Modified 13 February 2020
 *  By Balescu Ovidiu-Gheorghe
 */

#include "MotorDc.h"

/**
 *  @brief: This is copy constructor.
 *  
 *  @param source is MotorDc object.
 */
MotorDc::MotorDc (const MotorDc &source) {
   this->pinA = source.pinA;
   this->pinB = source.pinB;
   
   this->setSpeed (this->speedSignalIdle);
}

/**
 *  @brief: This is a constructor of MotorDc object.
 *
 *  @param: pinA - connected to first wire of MotorDc;
 *  @param: pinB - connected to second wire of MotorDc;
 *  @param: speedSignalBackward - signal of full backward speed;
 *  @param: speedSignalIdle - signal of stop;
 *  @param: speedSignalForward - signal of full forward speed.
 */
MotorDc::MotorDc (
    byte pinA,
    byte pinB,
    short speedSignalBackward,
    short speedSignalIdle,
    short speedSignalForward
) {
    pinMode(pinA, OUTPUT);
    pinMode(pinB, OUTPUT);

    this->pinA = pinA;
    this->pinB = pinB;

    this->setup (
        speedSignalBackward,
        speedSignalIdle,
        speedSignalForward
    );
    this->stop ();
}

/**
 *  @brief: This is a constructor of MotorDc object.
 *
 *  @param: pinA - connected to first wire of MotorDc;
 *  @param: pinB - connected to second wire of MotorDc;
 *  @param: speedSignalBackward - signal of full backward speed;
 *  @param: speedSignalIdle - signal of stop;
 *  @param: speedSignalForward - signal of full forward speed;
 *  @param: speed - speed of MotorDc. 
 */
MotorDc::MotorDc (
    byte pinA,
    byte pinB, 
    short speedSignalBackward,
    short speedSignalIdle,
    short speedSignalForward,
    short speed
) {
    pinMode(pinA, OUTPUT);
    pinMode(pinB, OUTPUT);

    this->pinA = pinA;
    this->pinB = pinB;

    this->setup (
        speedSignalBackward,
        speedSignalIdle,
        speedSignalForward
    );
    this->setSpeed (speed);
}

/**
 *  @brief: This is destructor of MotorDc object. 
 *  This stops the electronic signal to it.
 */
MotorDc::~MotorDc () {
   this->stop ();
}

/**
 *  @brief: .
 * 
 *  @param: speedSignalBackward - signal of full backward speed;
 *  @param: speedSignalIdle - signal of stop;
 *  @param: speedSignalForward - signal of full forward speed.
 */
void MotorDc::setup (
    short speedSignalBackward,
    short speedSignalIdle,
    short speedSignalForward
) {
    this->speedSignalBackward = speedSignalBackward;
    this->speedSignalIdle = speedSignalIdle;
    this->speedSignalForward = speedSignalForward;
}

/**
 *  @brief: This function sends signal to mantain speed of MotorDc.
 */
void MotorDc::loop () {
    if (this->speed >= this->speedSignalIdle) {
        analogWrite (pinA, this->speedSignalIdle);
        analogWrite (pinB, this->speed);
    }
    else {
        analogWrite (pinA, -this->speed);
        analogWrite (pinB, this->speedSignalIdle);      
    }
}

/**
 *  @brief: This function sends the signal to change speed of MotorDc.
 */
void MotorDc::setSpeed (short value) {
    this->speed = value;
}

/**
 *  @brief: This function stops move of MotorDc.
 */
void MotorDc::stop () {
    this->setSpeed (this->speedSignalIdle);
}

/**
 *  @brief: This function makes the MotorDc to move backward
 *  direction with full speed.
 */
void MotorDc::backward () {
    this->setSpeed (this->speedSignalBackward);  
}

/**
 *  @brief: This function makes the MotorDc to move forward
 *  direction with full speed.
 */
void MotorDc::forward () {
    this->setSpeed (this->speedSignalForward);
}

/**
 *  @brief: This function increases value of speed.
 */
void MotorDc::increaseSpeed (short rate) {
    if (this->speedSignalForward - rate <= this->speed) {
        this->setSpeed (this->speedSignalForward);
    }
    else {
        this->setSpeed (this->speed + rate);
    }
}

/**
 *  @brief: This function decreases value of speed.
 */
void MotorDc::decreaseSpeed (short rate) {
    if (this->speedSignalBackward + rate >= this->speed) {
        this->setSpeed (this->speedSignalBackward);
    }
    else {
        this->setSpeed (this->speed - rate);
    }
}

/**
 *  @brief: This change value of speed signal backward.
 *  
 *  @param: value - new value of speed signal backward.
 */
void MotorDc::setSpeedSignalBackward (short value) {
    if (this->speedSignalIdle > value) {
        this->speedSignalBackward = value;

        if (this->speedSignalBackward < this->speed) {
            this->backward ();
        }
    }
}

/**
 *  @brief: This change value of speed signal idle.
 *  
 *  @param: value - new value of speed signal idle.
 */
void MotorDc::setSpeedSignalIdle (short value) {
    if (this->speedSignalForward > value) {

        if(this->speedSignalBackward < value) {

            if (this->speedSignalIdle == this->speed) {
                this->setSpeed (value);
            }

            this->speedSignalIdle = value;
        }
    }
}

/**
 *  @brief: This change value of speed signal forward.
 *  
 *  @param: value - new value of speed signal forward.
 */
void MotorDc::setSpeedSignalForward (short value) {
    if (this->speedSignalIdle < value) {
        this->speedSignalForward = value;

        if (this->speedSignalForward < this->speed) {
            this->forward ();
        }
    }
}

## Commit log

2019-09-15 Small fixes and refactoring.
    [accountancy.ods, back.FCStd, configuration.txt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]
2019-09-23 Documentation and schematics
    [accountancy.ods, submarine.fzz]
2019-10-07 Update documentation
    [accountancy.ods, configuration.txt, submarine.fzz]
2020-02-25 Fix errors in modules and add details about software in documentation.
    [configuration.txt]
2020-03-15 Pull fix
    [submarine.fzz]
2023-02-24 Update readme, documentation and graphic interface.
    [Documentation.ods, config.txt, documentation.ods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]
2023-02-26 Updated readme, documentation and graphic interface.
    [Documentation.xlsx, Submarine.fzz, config.txt]
2023-05-20 Updated documentation
    [Documentation.xlsx]
2023-05-25 Updated the documentation, weight and cost
    [Documentation.xlsx]
2023-05-28 Update documentation, schematic and readme
    [Documentation.xlsx, Submarine.fzz]
